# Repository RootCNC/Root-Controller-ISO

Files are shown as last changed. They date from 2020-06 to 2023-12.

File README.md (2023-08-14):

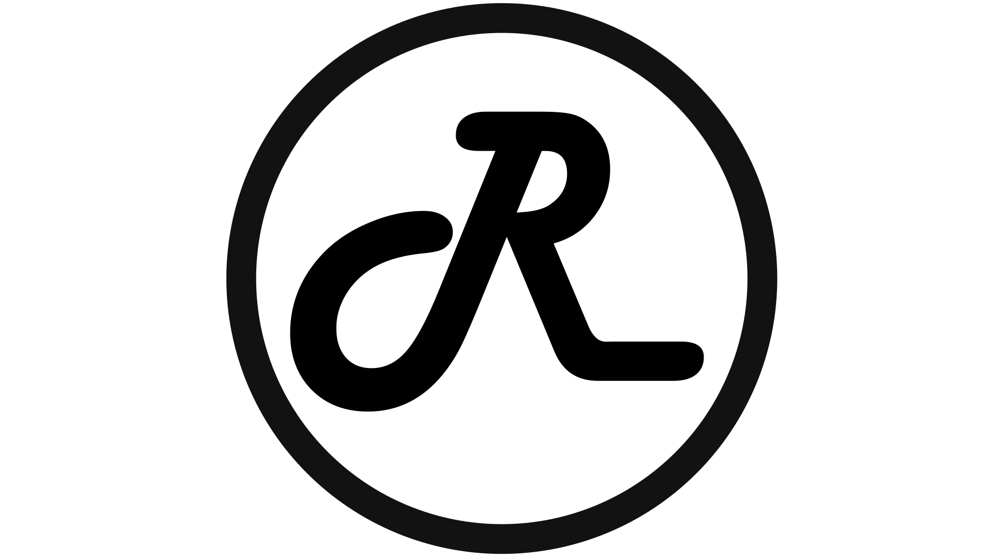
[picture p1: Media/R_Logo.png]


# About
At its core the Root controller is a ESP32 GRBL isolated motion controller (FluidNC). What makes this controller different is the focus of providing **isolated IO** to the **CNC controller**. The controller is designed to accommodate a wide range of operating conditions and machines, to provide ultimate flexibility (its not just a Root CNC Controller).

The controller is designed to isolate the key area of the design to mitigate any nuisance issues when operating in an electrically noisy environment. The design isolates the following areas from one another: Steppers driver outputs (achieved by using externally OPTO isolated drivers), USB, Relays, MOSFETs and RS485. Perfectly suited for the larger CNC machines. 

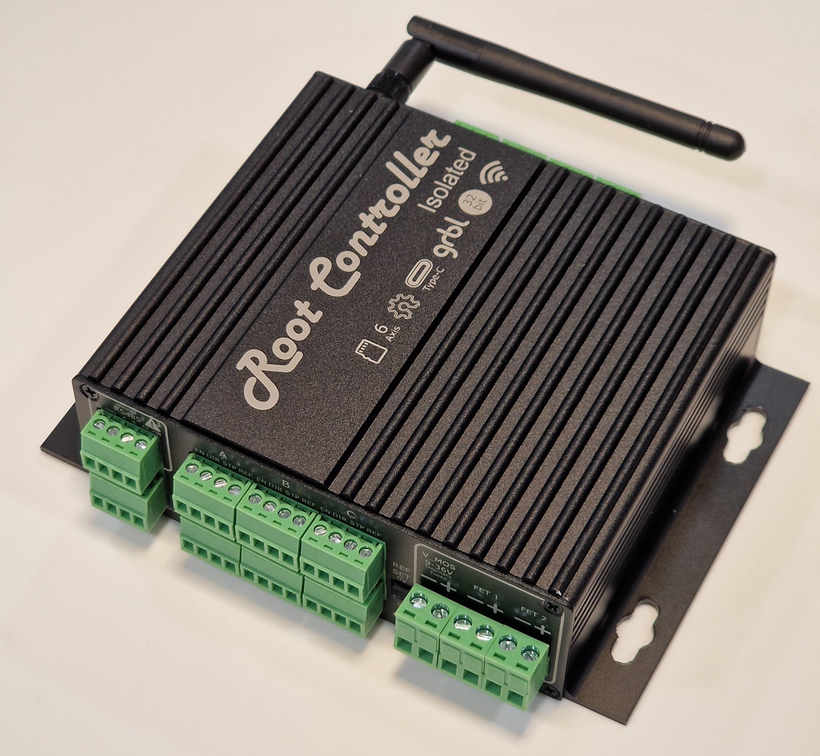
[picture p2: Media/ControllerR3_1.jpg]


## Key features 
1. **6 axis motion control** (Axis ganging can be done via software - 18 digital outputs, can be repurposed)
2. **Wide input voltage** range (9-36V)
3. **Wifi or bluetooth** support for remote control and job loading
4. **SD card**
5. **8 isolated inputs** (supporting NPN inductive switches and Standard NC/NO switches)
6. **2 isolated Relay** outputs for switching high voltage outputs, say a compressor
7. **2 isolated MOSFET**, perfect for driving solenoids for coolant or mist
8. Dedicated **Laser output port**. 
9. **Isolated USB**
10. **Isolated RS485** (Modbus serial port)

## Block Diagram
Root Controller Overview Block Diagram

## Purchase
The Root Controller ISO can be purchased on the Root CNC store
[GOTO SHOP](https://rootcnc.com/product-category/electronics/)

## Demo Video
> Click Image to load youtube video
{.is-info}

Demo Video (https://youtu.be/JiuDgxlzHaU "Video Title")

## Electrical Specification 
Details can be found [**here**](https://wiki.rootcnc.com/en/Root-Controller-ISO/DetailedInfo). If you require additional information I have missed, please contact me and I'll get it added.
## Wiring information
For more information on how to wire and connect the Root Controller to external drives, sensors and other peripherals. please see the Wiki site. [Link to the WIKI](https://wiki.rootcnc.com/en/Root-Controller-ISO/DetailedInfo)
## Software pinouts
To control the hardware the pinout of peripherals needs to be known, the link **[here](https://wiki.rootcnc.com/en/Root-Controller-ISO/DetailedInfo)** is a convenient way to map Input and Output to the software.
## Software Configurations
For basic configurations for your machine, please see the sub folder names "Configurations"

## Mechanical dimensions

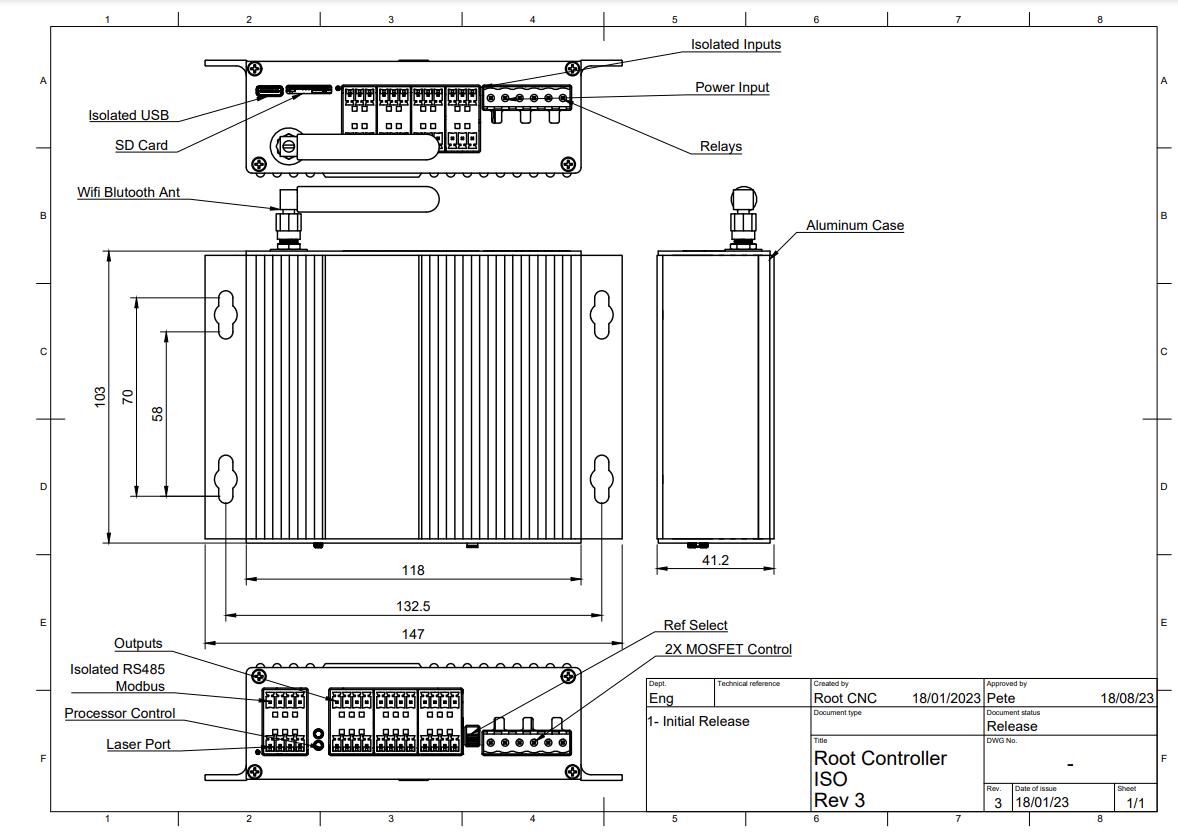
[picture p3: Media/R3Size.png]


## PCB layout

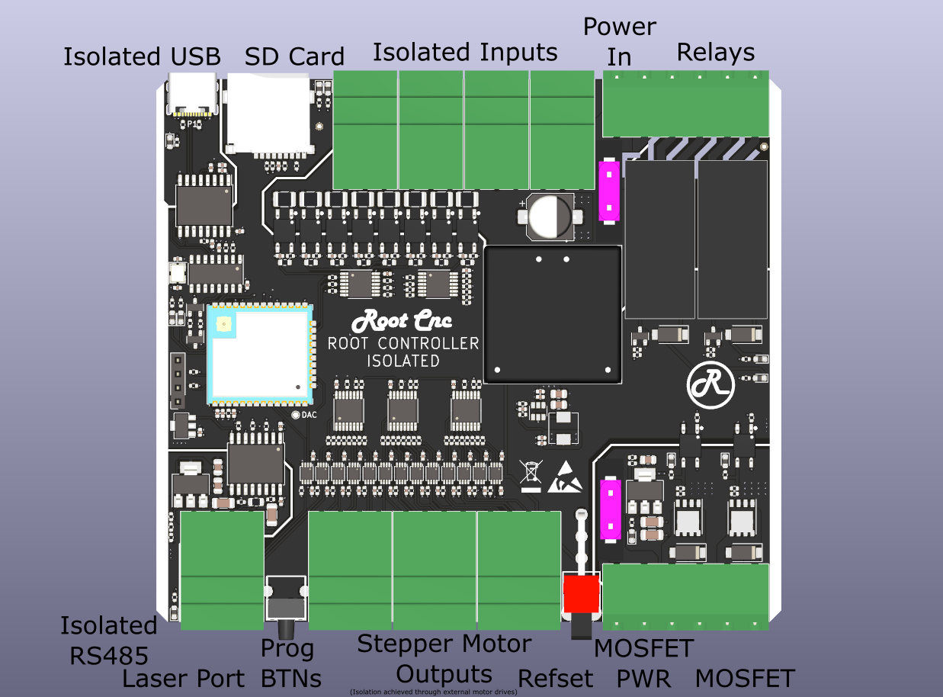
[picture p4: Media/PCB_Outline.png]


## What is Root CNC
For Root CNC project information 
visit [the website](https://rootcnc.com)
## Social links

 1. [Facebook Group](https://www.facebook.com/groups/rootcnc/) 
 2. [Discourse](https://rootcnc.discourse.group/) 
 3. [Discord](https://discord.gg/93Ue5SwthW) Great for quick answer to questions and firmware support
 4. [Thingiverse](https://www.thingiverse.com/sailorpete/designs) 
 5. [Youtube](https://www.youtube.com/c/sailorpete12/)

## License

This project is licensed under the Creative Commons 4.0 license with 
Attribution-NonCommerial-ShareAlike see `LICENSE.txt` for details

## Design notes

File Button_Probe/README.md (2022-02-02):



# About
Easy way to add convenient buttons to your CNC Machine. It offers buttons for common actions like, Hold, Start, Macro. it also offers a easy accessible probe point via 4mm banana plugs
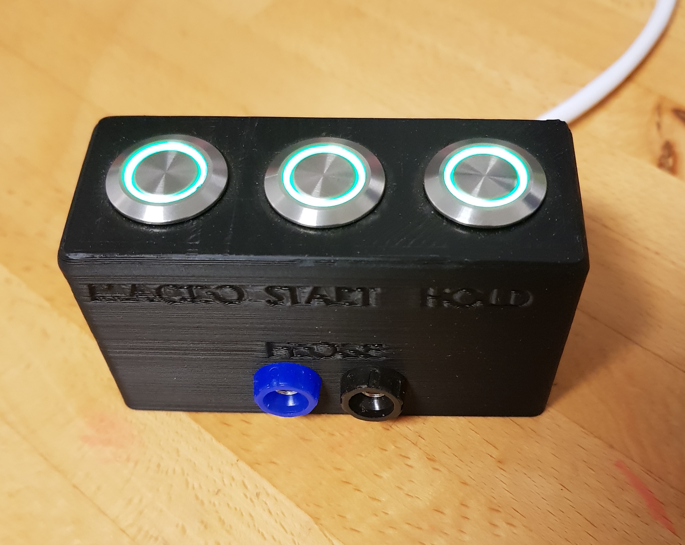
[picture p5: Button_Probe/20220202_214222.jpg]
Root Controller Render


## Key features 
1. Easy breakout and wiring of frequently used buttons and probe mount
2. Built in current limit resistors for LED button

## Require Parts
The product requires parts to be sourced or printed externally
1. Single Pole Single Throw (SPST) Momentary LED Push Button 16mm Dia x3
2. 4mm Banana terminals x2
3. Printed case (Top and bottom)
4. 3mm insert nuts (The kind you use the soldering Iron with) x6
5. 3mm x 6mm Bolts x4
6. 3mm x 10mm Bolts x2

## Purchase
The Root Controller Buttons can be purchased on the Root CNC store
[GOTO SHOP](https://rootcnc.com/product-category/electronics/)

## What is Root CNC
For Root CNC project information 
visit [the website](https://rootcnc.com)
## Social links

 1. [Facebook Group](https://www.facebook.com/groups/rootcnc/) 
 2. [Discourse](https://rootcnc.discourse.group/) 
 3. [Discord](https://discord.gg/93Ue5SwthW) Great for quick answer to questions
 4. [Thingiverse](https://www.thingiverse.com/sailorpete/designs) 
 5. [Youtube](https://www.youtube.com/c/sailorpete12/)

## License

This project is licensed under the Creative Commons 4.0 license with 
Attribution-NonCommerial-ShareAlike see `LICENSE.txt` for details

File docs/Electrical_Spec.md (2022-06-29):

# Root Controller ISO Electrical characteristics
This section is split up into the isolation zones of the controller.

For more information on the different isolation zones, please see the Wiki page tilted "Power" [Link Here](https://wiki.rootcnc.com/en/RootControllerPower)

## Primary PSU
### PSU
This is denoted a `V` and `0V_V` for supply and return respectively on the case sticker.
Power is applied through its own dedicated fused port. 

| **Parameter** | **Min** | **Typ** | **Max** |**Unit**|
|--|--|--|--|--|
| Vin (`V` wrt `0V_V`) | 9 |24|36|V|
|Current (Fuse Protected) (*1)|  |0.86|(*2)|A|
|Input Isolation voltage  [`V` vs `0V`(*3)]| 1.5 |||KV
-   (*1) – This is current draw of the Root CNC controller including worst case power export via output pins. This does not induce the exported power on V pins (Such as powering inductive probes)
- (*2) - Installed fuse is TBD
-  (*3) – 0V is the isolated floating voltage on the Root CNC controller – Do Not connect this to chassis

### Input
The inputs to the Root controller are referenced to the `0V_V` of the Primary PSU. All input are isolated to the rest of the system.

The Input are arranged to accept either an Open-Collector/ Open-Drain switch or a standard mechanical switch. Depending on the Primary PSU voltage this switching current will vary. 
| **Parameter** | **Condition** |**Min** | **Typ** | **Max** |**Unit**|
|--|--|--|--|--|--|
| Switching Current |(*1) |2.7||10|mA|
| |V = 12V ||2.7||mA|
|  |V = 24V ||5.8||mA|
|  |V = 36V ||8.9||mA|

* (1) Over full operating conditions 
# RS485 
This section is denoted by `V_RS` and `0V_RS` respectively for the Power in and 0V for the isolated RS485 port. 

| **Parameter** | **Min** | **Typ** | **Max** |**Unit**|
|--|--|--|--|--|
| Vin (`V_RS`wrt `0V_RS`) | 8.1 |12|36|V|
|Current Draw |  |1.6|2|mA|
|Basic DC Isolation  [`V_RS` vs `0V`]| ||1.517|KV
|Reinforced DC Insulation  [`V_RS` vs `0V`] (*1)| ||0.757|KV
|Basic bipolar AC Isolation  [`V_RS` vs `0V`] (*1)| ||565|V
|Reinforced bipolar AC Insulation  [`V_RS` vs `0V`] (*1)| ||565|V
|Differential Input Threshold Voltage, Vth|-200 |-125|-30|mV
|Input Hysteresis|| 20|| mV
|Input Resistance (A, B) (*2) |96 |150|| kΩ
|Output High Voltage|4.6|4.9||V
|Output Low Voltage||0.1|0.4|V
|Output Short-Circuit Current| 7| |85| mA
|ESD Rating (`A`,`B`)||HMB (+/-2KV)

* (1) Maximum Continuous Working Voltage
* (2) RS485 does not contain a bus termination resistor - place provisioned. The Isolating RS485 has internal thresholds to detect logic levels. 

# Digital Output
Isolation is achieved by using Opto-Isolated Stepper motor drivers

|**Parameter**|**Min**|**Typ**|**Max**|**Unit**|
|--|--|--|--|--|
|Vout (Root controller derived supply)|4.95|5|5.05|V
|Output current|||150|mA
|IOH High-level output current (*1)|||25|mA
|IOL Low-level output current (*1)|||25|mA
|VOH High-level output voltage (*2)|3.8|||V
|VOL Low-level output voltage (*3)|||0.55|V

-   (*1) This parameter makes the Root CNC controller extremely well suited to drive opto-isolated stepper motor drivers (special sauce)
-   (*2) – Over full operating specification and at max current draw (-32mA)
-   (*3) – Over full operating specification and at max current draw (32mA)

# MOSFET Isolation
The Root Controller provides three MOSFET controller switches. These switches have their own dedicated input power supply and can be driven from a separate PSU or the same PSU as `V` to allow for greater flexibility.

| **Parameter** | **Min** | **Typ** | **Max** |**Unit**|
|--|--|--|--|--|
| Vin (`V_F` wrt `0V_F`) | 12|15|36|V|
|Current (Fuse Protected) (*1)|0.001  ||(*2)|A|
* (1) Current is dependant of the peripherals you connect to the controller
* (2) Controller has an internal fuse - Rating is TBD

# Relay 
The Root controller has three NO relays (the Normally closed Pole is not accessible). These are design to allow the user to switch large main powered loads, such as Dust extraction, compressors and even lighting.
| **Parameter** | **Min** | **Typ** | **Max** |**Unit**|
|--|--|--|--|--|
| Switch Voltage DC| ||300|V|
| Switch Voltage AC| ||440|V|
|Contact Resistance|||100|mOhm|
|Switch Current (Resistive Load)|||12|A|
|Max Switch Power|||3000|VA|
|Endurance (Switch Cycles)|||1x10^7||

# USB
The USB port on the Root controller is a Type-C 2.0 UFP. This port is also isolated with the `0V`

| **Parameter** | **Min** | **Typ** | **Max** |**Unit**|
|--|--|--|--|--|
| Voltage (`V_USB` to `0V_USB`) |4.5 |5|5.5|V|
| Current| 5|8|10|mA|
| Data Rate| ||12|Mbps|
|DC Basic Isolation  |||849|V|
|AC Bipolar Basic Isolation  |||849|V|
|AC Unipolar Basic Isolation  |||560|V|

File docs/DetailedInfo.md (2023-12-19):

---
title: About
description: Root Controller ISO About
published: true
date: 2022-03-18T14:52:57.756Z
tags: cnc controller, root controller, motion controller, isolation
editor: markdown
dateCreated: 2022-02-25T22:12:57.077Z
---

# Introduction


At its core the Root controller is a ESP32 GRBL isolated motion controller (FluidNC/ grblHAL). What makes this controller different is the focus of providing  **isolated IO** to the **CNC controller**. The controller is designed to accommodate a wide range of operating conditions and machines, to provide ultimate flexibility (its not just a Root CNC Controller).

The controller is designed to isolate the key area of the design to mitigate any nuisance issues when operating in an electrically noisy environment. The design isolates the following areas from one another: Steppers driver outputs (achieved by using externally OPTO isolated drivers), USB, Relays, MOSFETs and RS485. Perfectly suited for the larger CNC machines. 

## Key features 



1. **6 axis motion control** (Axis ganging can be done via software - 18 digital outputs, can be repurposed)
2. **Wide input voltage** range (9-36V)
3. **WiFi or bluetooth** support for remote control and job loading
4. **SD card**
5. **8 Isolated inputs** (supporting NPN inductive switches and Standard NC/NO switches)
6. **2 Isolated Relay** outputs for switching high voltage outputs, say a compressor
7. **2 isolated MOSFET**, perfect for driving solenoids for coolant or mist
8. Dedicated **Laser output port**. 
9. **Isolated USB**
10. **Isolated RS485** (Modbus serial port)

## Block Diagram
Root Controller Overview Block Diagram

## Demo Video
# Tabs {.tabset} 
> Click Image to load youtube video
{.is-info}

## Rev 3

Demo Video (https://youtu.be/JiuDgxlzHaU "Root Controller Rev 3")

## Rev 2.1/2.0

Demo Video (http://www.youtube.com/watch?v=vrsv_Eusyqc "Root Controller Rev 2")

# Power
The Root controller is segregation into multiple isolation zones to suit the individual needs of the CNC builder. The purpose of these zones is to help isolated areas from interfering with one another. For example the spindle control vs the low noise CNC controller zones. The Root controller is well suited for large CNC machines and plasma cutters.

Carefully consideration should be made when planning the electronics for your CNC machine. As optimal performance is dependent on the type of machine you are building. The information below will aid your design. If you feel information is missing, please send me a message and I’ll clarify and aid you.

The controller has the following major areas of isolation:
1. `V_in ISO` - this is used for all inputs and powering the CNC motion controller.
2. `RS-485 isolation zone` - this provides an isolated RS485 interface to talk to your VFD or other peripherals (more items will be added in the future). This zone is typically powered by the VFD and doesn’t require any additional interfaces or PSUs
3. `MOSFET isolation` - this is a separation isolated zone which comprised of three high power MOSFETs. This is powered from a separate power input and is perfect for controlling device which need power, for example Solenoids, lights etc
4. `Controller reference` - this area is not isolated to the CNC controller. isolation is achieved through the OPTO isolated stepper motor drivers. The laser/ spindle port is also referenced to this area. when using this port, careful consider is required to ensure the other isolation zones are not violated.
5. `Relay zone` - three relay outputs are inherently isolated from everything else and between them self.
6. `USB ISO` - the usb type C connector is isolated from the controller to ensure. This is perfect to ensure your expensive laptop or CNC computer is not directly attached to your machine, this help mitigate fault propagation effecting you machine. 
# Tabs {.tabset}
## Rev 3



## Rev 2.1/2.0
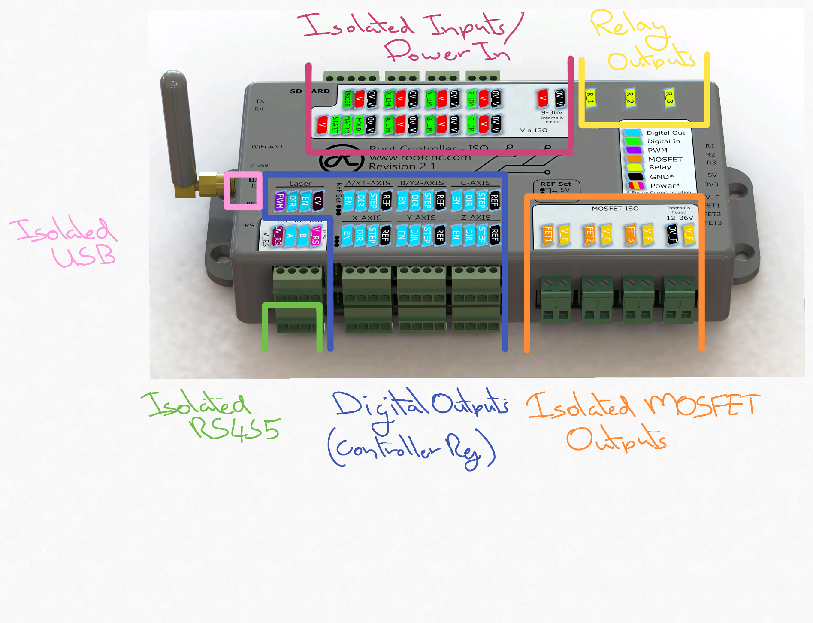
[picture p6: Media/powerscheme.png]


> To ensure optimal performance and noise immunity - please ensure the current return paths and loops are reduced and power zone references are not connected together. E.g. avoid connecting `0V` to `0V_V` 
{.is-warning}

# Powering the controller
Power is applied through the power in connector in the `Vin ISO` zone. The input requires a supply voltage of anything between 12-36v. 

This power supply is internally fused for added protection.

The minimum PSU capacity should greater then `8 watts` to power the controller.

The voltage applied to the controller through this connector is also applied to the controllers inputs power pins. This is useful when powering external sensors, such as inductive probes. The inputs power pins are fused with the same fuse as the main input power connector. 

# Tabs {.tabset}
## Rev 3



## Rev 2.1/2.0
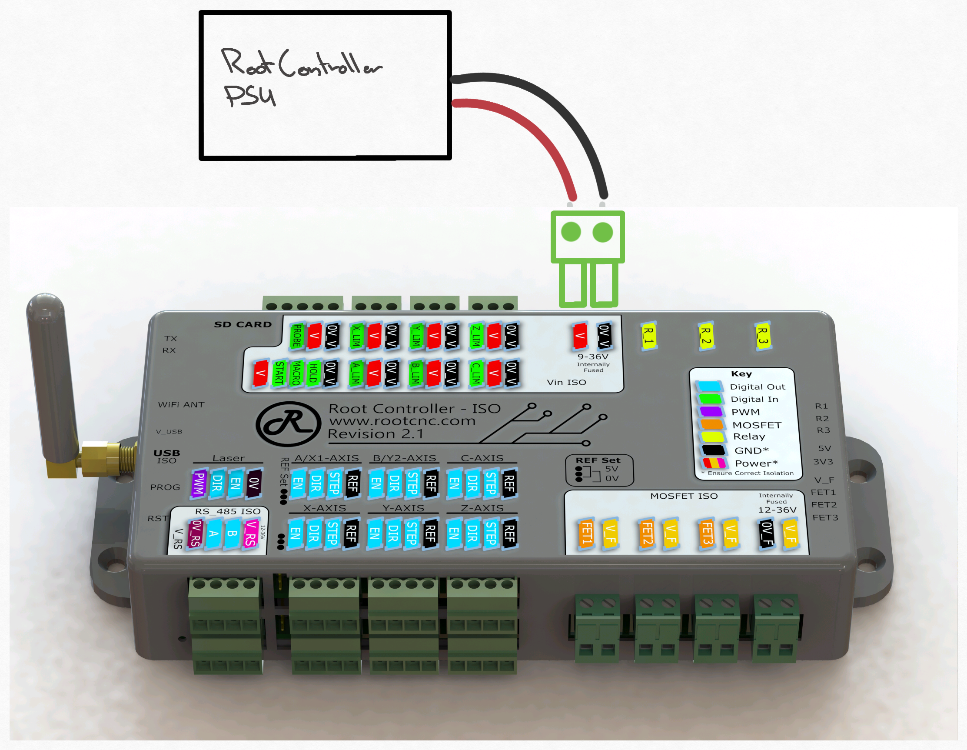
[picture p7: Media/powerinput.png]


# Stepper control
The Root Controller is specifically designed to control **OPTO isolated external stepper motor drivers**. The reason for this is due to their high current demands of their logic inputs on the motor driver, these are typically around 10-20mA per input (enable signals are typically lower as these do tend not to toggle). These sort of current demands normally exceeds the max electronic IC package current. Exceeding these values can impact the life of the electronic products - the Root controller ISO has been designed to take this into account and will happily supply the max current across all its outputs and provide a long life for the electronics.

The Root controller Rev `2.1` and onwards supports both `common Anode` and `common Cathode` external motor drivers, with the use of the `ref set` settings. 

| Drive type | Rev 3 | Rev 2.1 | Rev 2.0  |
|---|---|---|---|
| Common Annode  | Yes | Yes | NO |
| Common Cathode | Yes | Yes | Yes |

>Some drivers might expose both anode and cathode per input, if this is the case then the wiring will need to be configured into either common anode or common cathode. please see example wiring configurations for more information
{.is-info} 

## Stepper Driver Outputs
The Root controller support six software configurable stepper motor outputs. These are accessable via a 4 port connector, which are wired identically.
## Tabs {.tabset}
### Rev 3



### Rev 2.1/2.0


When not using these ports for the stepper motor controller, then the remaining ports can be reconfigured in software to support discrete outputs.

## Ref Set 
> The Root Controller has two configurable references, either 0V or 5V to set the refernece point for either common anode or cathode stepper motor wiring. please ensure these are correctly configured. More information below. (Rev 2.1 and onwards) {.is-info} 

## Tabs {.tabset}
### Rev 3



### Rev 2.1
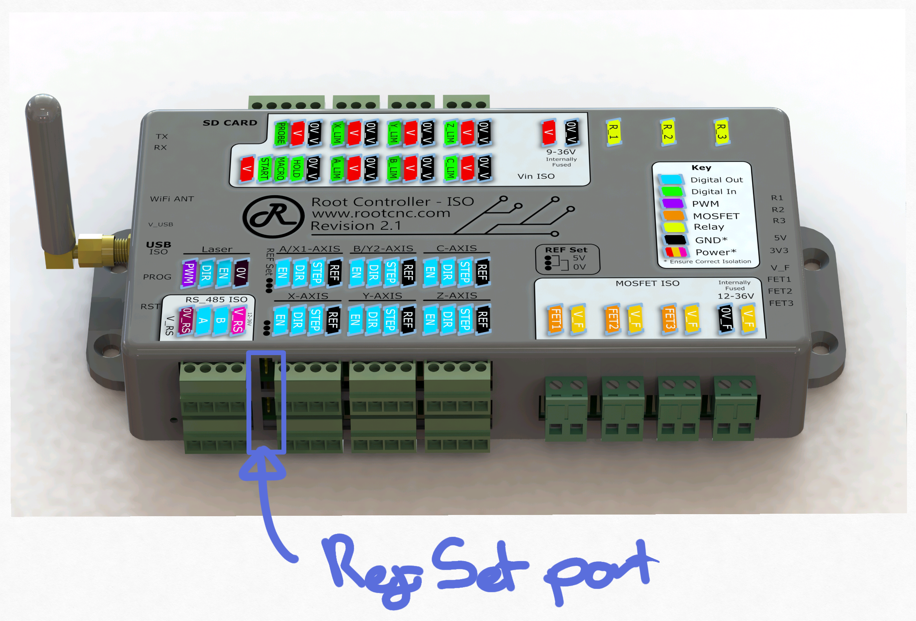
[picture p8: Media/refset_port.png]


Both headers on the Root Controller need to be set correctly in order for correct operation, these are denoted as `ref set` on the controller label. You can mix the top and bottom reference points but you’ll need to ensure the three outputs per layer are set correctly with the corresponding outputs. Its recommended to set the ref set points to same configurations.

- Ref set 1 - sets the reference point for axis outputs X, Y, Z
- Ref set 2 - sets the reference point for axis outputs A, B, C
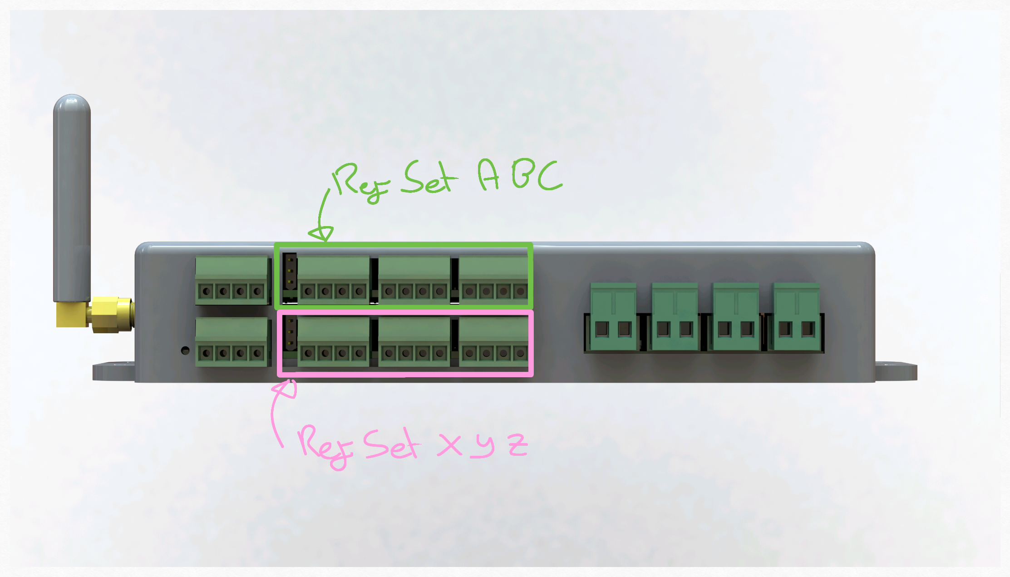
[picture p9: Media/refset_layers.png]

> Please note these outputs are software configurable. The Root 3 onwards will use either axis outputs of A, B, C to be the second Y (YII) axis. If you are planning on using the root controller for other style of machines; the software supports up to two outputs per axis. For example the MPCNC Which has XII and YII which will use ports A,B.{.is-info} 

### Rev 2.0
>` Rev 2.0` only supports a common cathode (0V reference) {.is-warning}

### Beta Card

> Beta card can accommodate both common anode and common cathode by default{.is-info} 

## Stepper Motor Driver Wiring
### 5V reference (Common Anode)
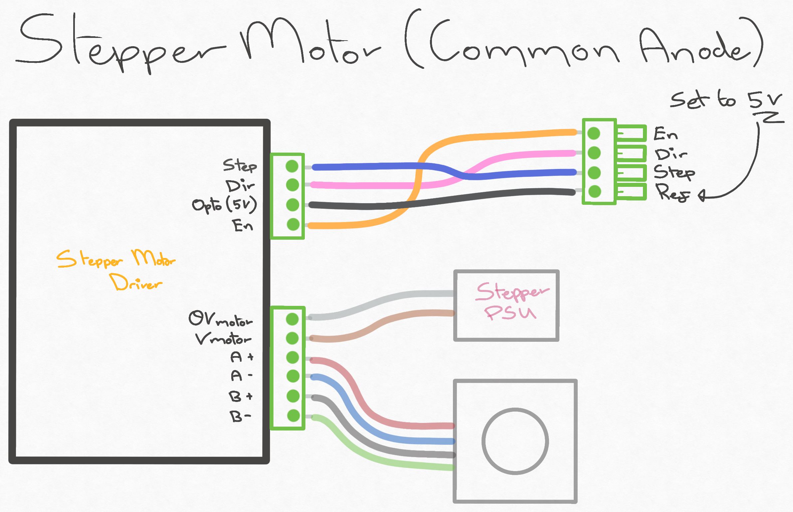
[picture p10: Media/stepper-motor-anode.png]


Below is a list of known external motor drivers to work in the common anode configuration:
* DM320
* DM332

Using this configuration results in the logic being inverted - please configure the software to be either Rising or falling edge triggered or your machine could be half a step out continuously 

### 0V reference (Common Cathode)
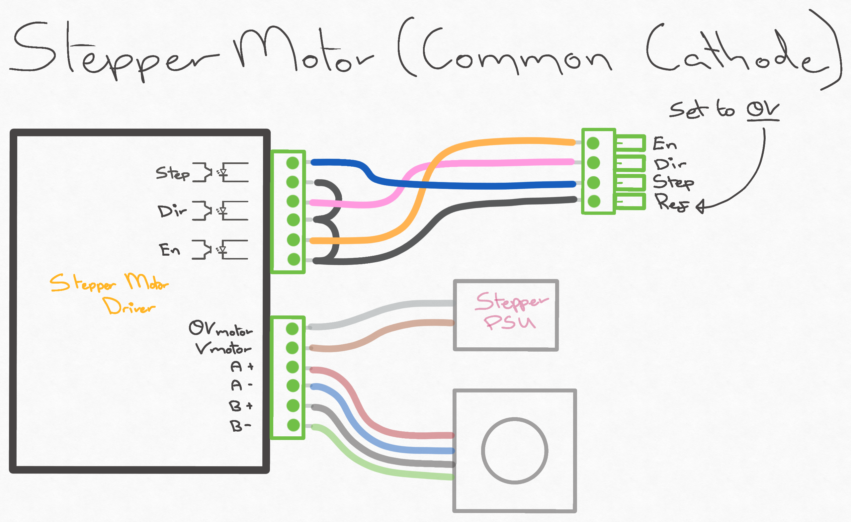
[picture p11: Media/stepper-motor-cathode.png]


Below is a list of known external motor driver to work in the common cathode arrangement

>  My Root 4 and 4 Lite both use the common cathode setup

* DM542
* DM556
* DM860

#### Fuildnc motor configuration (Common Cathode)

#### Tabs {.tabset}

##### X Motor


```
      x:
        steps_per_mm: 160.000
        max_rate_mm_per_min: 4500.000
        acceleration_mm_per_sec2: 500.000
        max_travel_mm: 100
        soft_limits: true
        homing:
          cycle: 1
          positive_direction: true
          mpos_mm: 100
          feed_mm_per_min: 100.000
          seek_mm_per_min: 800.000
          settle_ms: 500
          seek_scaler: 1.100
          feed_scaler: 1.100
    
        motor0:
          limit_neg_pin: NO_PIN
          limit_pos_pin: NO_PIN
          limit_all_pin: NO_PIN
          hard_limits: true
          pulloff_mm:1.000
          standard_stepper:
            step_pin: I2SO.7:low 
            direction_pin: I2SO.5:low 
            disable_pin: I2SO.3:high
```

Motor definition for the X motor port

##### Y Motor



```
  y:
    steps_per_mm: 160.000
    max_rate_mm_per_min: 4500.000
    acceleration_mm_per_sec2: 500.000
    max_travel_mm: 100.000
    soft_limits: true
    homing:
      cycle: 1
      positive_direction: true
      mpos_mm: 100
      feed_mm_per_min: 100.000
      seek_mm_per_min: 800.000
      settle_ms: 500
      seek_scaler: 1.100
      feed_scaler: 1.100

    motor0:
      limit_neg_pin: NO_PIN
      limit_pos_pin: NO_PIN
      limit_all_pin: NO_PIN
      hard_limits: true
      pulloff_mm:1.000
      standard_stepper:
        step_pin: I2SO.12:low 
        direction_pin: I2SO.10:low 
        disable_pin: I2SO.8:high
```

Motor definition for the Y motor port

##### Z Motor



```
  z:
    steps_per_mm: 160.000
    max_rate_mm_per_min: 4500.000
    acceleration_mm_per_sec2: 500.000
    max_travel_mm: 100.000
    soft_limits: true
    homing:
      cycle: 1
      positive_direction: true
      mpos_mm: 100
      feed_mm_per_min: 100.000
      seek_mm_per_min: 800.000
      settle_ms: 500
      seek_scaler: 1.100
      feed_scaler: 1.100

    motor0:
      limit_neg_pin: NO_PIN
      limit_pos_pin: NO_PIN
      limit_all_pin: NO_PIN
      hard_limits: true
      pulloff_mm:1.000
      standard_stepper:
        step_pin: I2SO.18:low 
        direction_pin: I2SO.16:low 
        disable_pin: I2SO.14:high
```

Motor definition for the Z motor port

##### A Motor



```
  a:
    steps_per_mm: 160.000
    max_rate_mm_per_min: 4500.000
    acceleration_mm_per_sec2: 500.000
    max_travel_mm: 100.000
    soft_limits: true
    homing:
      cycle: 1
      positive_direction: true
      mpos_mm: 100
      feed_mm_per_min: 100.000
      seek_mm_per_min: 800.000
      settle_ms: 500
      seek_scaler: 1.100
      feed_scaler: 1.100

    motor0:
      limit_neg_pin: NO_PIN
      limit_pos_pin: NO_PIN
      limit_all_pin: NO_PIN
      hard_limits: true
      pulloff_mm:1.000
      standard_stepper:
        step_pin: I2SO.6:low 
        direction_pin: I2SO.4:low 
        disable_pin: I2SO.2:high
```

Motor definition for the A motor port

##### B Motor



```
  b:
    steps_per_mm: 160.000
    max_rate_mm_per_min: 4500.000
    acceleration_mm_per_sec2: 500.000
    max_travel_mm: 100.000
    soft_limits: true
    homing:
      cycle: 1
      positive_direction: true
      mpos_mm: 100
      feed_mm_per_min: 100.000
      seek_mm_per_min: 800.000
      settle_ms: 500
      seek_scaler: 1.100
      feed_scaler: 1.100

    motor0:
      limit_neg_pin: NO_PIN
      limit_pos_pin: NO_PIN
      limit_all_pin: NO_PIN
      hard_limits: true
      pulloff_mm:1.000
      standard_stepper:
        step_pin: I2SO.13:low 
        direction_pin: I2SO.11:low 
        disable_pin: I2SO.9:high
```

Motor definition for the B motor port

##### C Motor



```
  c:
    steps_per_mm: 160.000
    max_rate_mm_per_min: 4500.000
    acceleration_mm_per_sec2: 500.000
    max_travel_mm: 100.000
    soft_limits: true
    homing:
      cycle: 1
      positive_direction: true
      mpos_mm: 100
      feed_mm_per_min: 100.000
      seek_mm_per_min: 800.000
      settle_ms: 500
      seek_scaler: 1.100
      feed_scaler: 1.100

    motor0:
      limit_neg_pin: NO_PIN
      limit_pos_pin: NO_PIN
      limit_all_pin: NO_PIN
      hard_limits: true
      pulloff_mm:1.000
      standard_stepper:
        step_pin: I2SO.19:low 
        direction_pin: I2SO.17:low 
        disable_pin: I2SO.15:high
```

Motor definition for the Y motor port

##### X Dual Motors
Ganging two motors together can be implemented with the following motor definition:

> (In this example I use the X Motor and A motor port){.is-info}
```
  x:
    steps_per_mm: 160.000
    max_rate_mm_per_min: 4500.000
    acceleration_mm_per_sec2: 500.000
    max_travel_mm: 100
    soft_limits: true
    homing:
      cycle: 1
      positive_direction: true
      mpos_mm: 100
      feed_mm_per_min: 100.000
      seek_mm_per_min: 800.000
      settle_ms: 500
      seek_scaler: 1.100
      feed_scaler: 1.100

    motor0:
      limit_neg_pin: NO_PIN
      limit_pos_pin: NO_PIN
      limit_all_pin: NO_PIN
      hard_limits: true
      pulloff_mm:1.000
      standard_stepper:
        step_pin: I2SO.7:low 
        direction_pin: I2SO.5:low 
        disable_pin: I2SO.3:high
    motor1:
      limit_neg_pin: NO_PIN
      limit_pos_pin: NO_PIN
      limit_all_pin: NO_PIN
      hard_limits: true
      pulloff_mm:1.000
      standard_stepper:
        step_pin: I2SO.6:low 
        direction_pin: I2SO.4:low 
        disable_pin: I2SO.2:high
```
> Any axis can have ganged motors! upto a total of 6 motors per controller. This is an example axis configuration.{.is-info}

##### Y Dual Motors

Ganging two motors together can be implemented with the following motor definition. This configuration is used on the Root CNC series.
> (In this example I use the Y Motor and B motor port){.is-info}
```
  y:
    steps_per_mm: 160.000
    max_rate_mm_per_min: 4500.000
    acceleration_mm_per_sec2: 500.000
    max_travel_mm: 100.000
    soft_limits: true
    homing:
      cycle: 1
      positive_direction: true
      mpos_mm: 100
      feed_mm_per_min: 100.000
      seek_mm_per_min: 800.000
      settle_ms: 500
      seek_scaler: 1.100
      feed_scaler: 1.100

    motor0:
      limit_neg_pin: NO_PIN
      limit_pos_pin: NO_PIN
      limit_all_pin: NO_PIN
      hard_limits: true
      pulloff_mm:1.000
      standard_stepper:
        step_pin: I2SO.12:low 
        direction_pin: I2SO.10:low 
        disable_pin: I2SO.8:high
    motor1:
      limit_neg_pin: NO_PIN
      limit_pos_pin: NO_PIN
      limit_all_pin: NO_PIN
      hard_limits: true
      pulloff_mm:1.000
      standard_stepper:
        step_pin: I2SO.13:low 
        direction_pin: I2SO.11:low 
        disable_pin: I2SO.9:high
```
> Any axis can have ganged motors! upto a total of 6 motors per controller. This is an example axis configuration.{.is-info}

#### grblHAL motor configuration (Common Cathode)

#### Tabs {.tabset}

##### X Motor
Comming soon

##### Y Motor
Comming soon

##### Z Motor
Comming soon

##### A Motor
Comming soon

##### B Motor
Comming soon

##### C Motor
Comming soon

# Inputs
The Root controller ISO has isolated inputs which are referenced to the Vin section of the card. Please take note of the isolation boundaries when connecting up the inputs.

The Controller is designed to support normal volt-free switch; such as mechanical switches, either NC (normally closed) or NO (normally open); And/Or NPN inductive sensors. All inputs are electrically the same. For ease of wiring, all axis limit inputs have the same connector and pin out. 

The inputs which are used for “start”, “hold” and “macro” do have a different connector, so please take note of the difference in wiring. Again easy to wiring, Root CNC offer a easy button/ probe point PCB. These can be purchased from the store or downloaded from GitHub.

All inputs are software configured and can be repurposed.

| | Rev 3 | Rev 2.1 | Rev 2.0  |
|---|---|---|---|
| Axis Inputs | 6 | 6 | 6 |
| Probe Input | 1 | 1 | 1 |
| User Configurable  | 1 | 3 | 3 |

> Please note all input listed in the table are software configurable inputs which can be used for any function.



- axis inputs (one per axis, min and max can be combined onto on input. Please see the end stop section for more information)
- x1 probe point (used to auto tool height correction of edge finding)
- user configurable inputs (these are typically used for GRBL control signals such as Start, Hold, Reset and Macros.

## Endstops
As mentioned in the pervious section, the Root controller is designed to accommodate voltage free switches, such as mechanical lever switches or NPN inductive switches.

Each input can have two sensors/ switches connected to it, these are typically used on axis with min and max limit switches.

### Inductive Probe Wiring 
> NPN Inductive Switch sensor ONLY {.is-info}

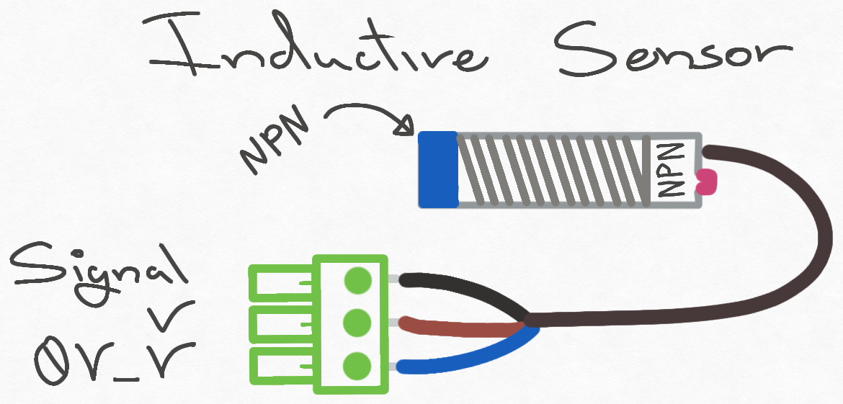
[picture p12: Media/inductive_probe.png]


### Inductive Probe Min & Max Wiring 
Image comming soon

### Basic Endstop Wiring
In this basic configuration, either NO (Normally Open) Or NC (Normally Closed) switches can be used
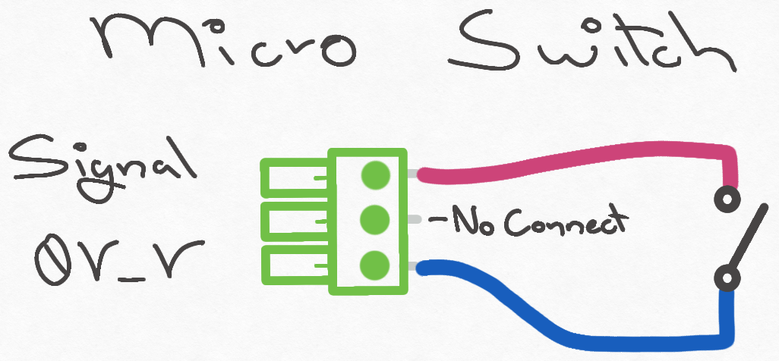
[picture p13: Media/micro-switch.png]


### Endstop wiring Min & Max (NO)
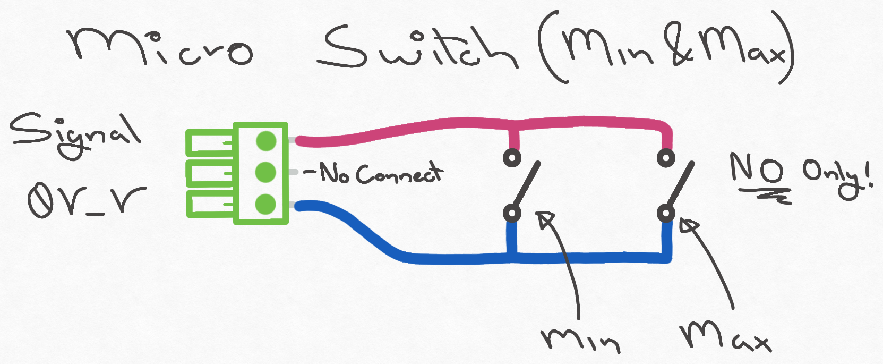
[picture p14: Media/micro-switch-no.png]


### Endstop wiring Min & Max (NC)
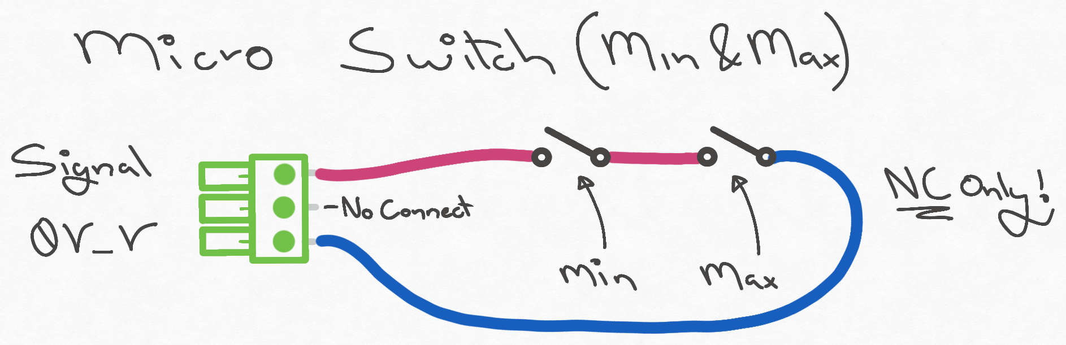
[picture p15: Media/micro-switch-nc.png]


> Please note REV 2.1/REV 2.0 - NC switches are not recommend on `Y_lim`. IF YOU INTEND TO FLASH THE ROOT CONTROLLER WHILST BEING INSTALLED IN A SYSTEMS. pulling these pins LOW stops the programming routing. If you do use NC switched: then, please ensure these are disconnected piror to programming. 
{.is-warning}

# Outputs
Aside from the digital outputs of the stepper driver port (Please see # Stepper control for more information). The Root Controller has the additional outputs:

| | Rev 3 | Rev 2.1 | Rev 2.0 |
|---|---|---|---|
|  MOSFET output (Isolated control) | 2 | 3 | 3 |
| High power relays | 2 | 3 | 3 |
| Laser/ spindle port (none isolated) | PWM, DIR, EN | PWM, DIR, EN | PWM, DIR, EN  |

- MOSFET output, great for turning lights or solenoids  on/off
- High power relays output, perfectly suited for turning shop vacs on or dust extractors
- Laser/ spindle port, perfect for controlling a PWM device

## MOSFETS
The Root controller has a number of high power MOSFETs which can be used to switch the power to a number of device, such as solenoids, lights and DC motors. 

The power supply is fed by its dedicated power connector. The input power is internally fused for added protection. The supply can be separate or tied to other supplies depending on your configuration.

The MOSFET area is perfectly suited for switching inductive loads such a solenoids or relays. 

| | Rev 3 | Rev 2.1 | Rev 2.0 |
|---|---|---|---|
|  PWM 															  | 1 (FET_1) | 2 (FET_1/2)  | 2 (FET_1/2) |
|  ON/ OFF controller								  | 1 | 1 | 1 |
|  **Total** 														  | **2** | **3** | **3** |

MOSFET control = on/off control and PWM control (Hardware dependant)

## Tabs {.tabset}
### Rev 3



> Please note depending on the software configuration, not all MOSFET or RELAY output can be used at the same time.
{.is-info}
### Rev 2.1/2.0


MOSFET control
- FET_1 - on/off control
- FET_2 - on/off control 
- FET_3 - on/off control

> Please note depending on the software configuration, not all MOSFET or RELAY output can be used at the same time.
{.is-info}

## Relay output 
The Root controller has a number relays outputs which can be used to switch high power loads, such as dust extractors, fume extractors and vacum cleaners. 

These relays are capable of switching mains power with a current of 13A.

| | Rev 3 | Rev 2.1 | Rev 2.0 |
|---|---|---|---|
| On/ Off control Relau | 2 | 3 | 3 |

## Tabs {.tabset}
### Rev 3



> Please note depending on the software configuration, not all MOSFET or RELAY output can be used at the same time.
{.is-info}
### Rev 2.1/2.0



> Please note depending on the software configuration, not all MOSFET or RELAY output can be used at the same time.
{.is-info}

## PWM laser/ Spindle output
The Root controller has a discrete output port which can be used to control a number of different devices. For example: lasers, and discrete control spindles.

Laser/ Spindle control
- EN - on/off control
- DIR - on/off control 
- PWM - on/off control & PWM Control

## Tabs {.tabset}
### Rev 3



### Rev 2.1/2.0


> For spindle control, it is advised you use a MODBUS/ RS485 VFD and communicated through the isolated spindle interface.
{.is-info}

> This port is NOT isolated so careful consideration is needed when connecting external devices to ensure the isolation zones are not violated
{.is-warning}

# Isolated RS485
The Root controller offers a fully isolated RS485/ MODBUS interface. This interface allows communication between the controller and a VFD spindle motor (OR other device - Software dependant).

This interface is intended to be to a small isolated area which is powered form the VFD or downstream connected device. for full operating range, please see the electrical specification below.

All versions of the Root Controller ISO offer the isolated RS485 interface



> Please note this interface will not work unless externally powered {.warning}

Here is an example of the wiring for the RS485 interface on a huanyang VFD

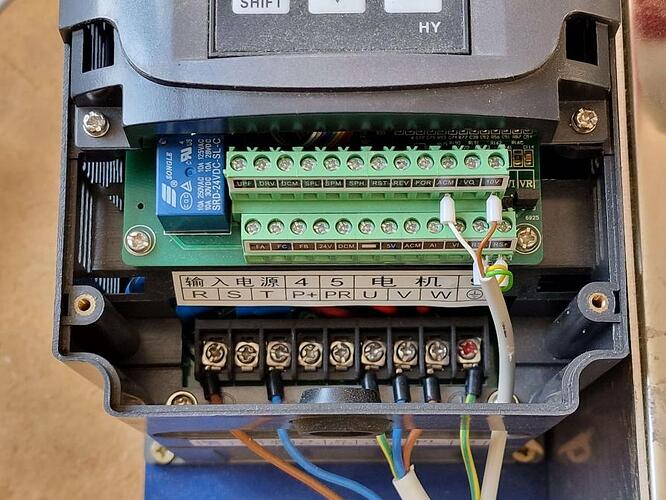
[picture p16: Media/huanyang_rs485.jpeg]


# SD CARD

The Root controller has expandable storage option in the form of an SD card. files can be sent over WIFI and stored on the SD for later use. this is particularly handy when running repetitive jobs. files can be accessed from a web browser over your local network.

For better compatibility, please use the older SD card rather than the newer ones.



All versions of the Root Controller ISO offer a SD card interface

To enable the code please use the following in the configuration

# Tabs {.tabset}
## Fluidnc

```
spi:
  miso_pin: gpio.19
  mosi_pin: gpio.23
  sck_pin: gpio.18

sdcard:
  card_detect_pin: NO_PIN
  cs_pin: gpio.5
```
## grblHAL

# WIFI / Blutooth

The Root controller offers wireless capability. this allows controller of the machine through your local network or via a mobile phone and blutooth. 

As EMC and isolation is a concern; careful positioning and placement of the antenna is critical for optimum performance. The Root Controller had implemented an internal antenna with the goal to reduce the cost of the controller. but this led to poor WIFI coverage; for this reason, the new versions of the Root controller offer an external antenna with can be extended using a standard SMA extension lead.



> Please note: the outer shield of the Antenna is connected to an internal reference plane. you **MUST NOT** connect this to Chassis or any other return planes as this will ruin your isolated setup. you will note the antenna port on the newer Rev 3 and onwards controllers has isolation washer between the case and the connector. This is to stop this connection from happening. If you intend to extend this internal for better antenna performance, or outside and electrical cabinet  - please ensure the isolation boundaries of isolation are kept. {.warning}

| | Rev 3 | Rev 2.1 | Rev 2.0 | Beta Card |
|---|---|---|---|---|
| WIFI Antenna  | External  | External  | Internal  | Internal  |

# Pin mapping
The Root controller comes in different forms, please select the tab that matches your hardware revision 
# Tabs {.tabset}
## ISO Rev 3

### I2S Output Port Mapping
I2S Bus is purely outputs ONLY.
| **Port**  |  **Description** |  **Port**  |  **Description** |  **Port**  |  **Description** |
|---|---|---|---|---|---|
| **I2S_0** | LASER_DIR | **I2S_8**  | Y_EN | **I2S_16** | Z_DIR |
| **I2S_1** | LASER_EN | **I2S_9**  | B_EN | **I2S_17** | C_DIR |
| **I2S_2** | A_EN | **I2S_10** | Y_DIR | **I2S_18** | Z_STEP |
| **I2S_3** | X_EN | **I2S_11** | B_DIR  		 | **I2S_19** | C_STEP |
| **I2S_4** | A_DIR			 | **I2S_12** | Y_STEP | **I2S_20** | RELAY_2 |
| **I2S_5** | X_DIR | **I2S_13** | B_STEP | **I2S_21** | RELAY_1 |
| **I2S_6** | A_STEP | **I2S_14** | Z_EN | **I2S_22** | FET_2 |
| **I2S_7** | X_STEP | **I2S_15** | C_EN | **I2S_23** | NOT USED |
{.dense}

### ESP32 Mapping
|**Port**| **Description**|**Port**| **Description**|**Port**| **Description**|
|--|--|--|--|--|--|
|**GPIO2**|P-PIN 	|**GPIO17**|RS_485_TX |**GPIO27**|Z-PIN  |  
|**GPIO4**|RS_485_DE_RE 	|**GPIO18**|SD_CLK |**GPIO32**|Y-PIN | 
|**GPIO5**|SD_CS 	|**GPIO19**|SD_MISO |**GPIO33**|LASER PWM |
|**GPIO12**|SHIFT_DATA 	|**GPIO21**|SHIFT_STR_CLK |**GPIO34**|X-PIN |
|**GPIO13**|FET_1 (PWM) |**GPIO22**|SHIFT_CLK |**GPIO35**| B-PIN |
|**GPIO14**|C-PIN 	|**GPIO23**|SD_MOSI |**GPIO36**|INTERNAL TEST POINT |
|**GPIO15**|*-PIN 	|**GPIO25**|INTERNAL TEST POINT |**GPIO39**|INTERNAL TEST POINT |
|**GPIO16**|RS_485_RX 	|**GPIO26**|A-PIN |||
{.dense}

## ISO Rev 2.0/2.1
> This list support the revision 2.0 Onwards. If you're after an earlier version pin out please see the version history on Github 
{.is-info}
### I2S Output Port Mapping
I2S Bus is purely outputs ONLY.
|**Port**| **Description**|**Port**| **Description**|**Port**| **Description**|**Port**| **Description**|
|--|--|--|--|--|--|--|--|--|--|
|**I2S_0**	|X_EN_PIN |**I2S_8**|Z_EN_PIN |**I2S_16**|	SPINDLE_DIR |**I2S_24**|	B_EN_PIN |
|**I2S_1**	|X_DIRECTION_PIN |**I2S_9**|Z_DIRECTION_PIN |**I2S_17**|	SPINDLE_EN |**I2S_25**|	B_DIRECTION_PIN|
|**I2S_2**	|X_STEP_PIN |**I2S_10**|	Z_STEP_PIN |**I2S_18**|	SPARE_1 |**I2S_26**|	B_STEP_PIN |
|**I2S_3**	|X_CS - NOT USED |**I2S_11**|	Z_CS - NOT USED|**I2S_19**|	SPARE_2 |**I2S_27**|	B_CS - NOT USED|
|**I2S_4**	|Y_EN_PIN |**I2S_12**|	FET_1 |**I2S_20**|	A_EN_PIN |**I2S_28**|	C_EN_PIN |
|**I2S_5**	|Y_DIRECTION_PIN |**I2S_13**|	RELAY_1 |**I2S_21**|	A_DIRECTION_PIN|**I2S_29**|	C_DIRECTION_PIN|
|**I2S_6**	|Y_STEP_PIN |**I2S_14**|	RELAY_2 |**I2S_22**|	A_STEP_PIN |**I2S_30**|	C_STEP_PIN |
|**I2S_7**	|Y_CS - NOT USED |**I2S_15**|	RELAY_3 |**I2S_23**|	A_CS - NOT USED|**I2S_31**|	C_CS - NOT USED|
{.dense}

### ESP32 Mapping
|**Port**| **Description**|**Port**| **Description**|**Port**| **Description**|
|--|--|--|--|--|--|
|**GPIO2**|Y-PIN 	|**GPIO17**|RS_485_TX |**GPIO27**|PROBE-PIN  |  
|**GPIO4**|RS_485_DE_RE 	|**GPIO18**|SD_CLK |**GPIO32**|B-PIN | 
|**GPIO5**|SD_CS 	|**GPIO19**|SD_MISO |**GPIO33**|FET_2 |
|**GPIO12**|SHIFT_DATA 	|**GPIO21**|SHIFT_STR_CLK |**GPIO34**|GRBL_MACRO |
|**GPIO13**|FET_3 	|**GPIO22**|SHIFT_CLK |**GPIO35**| A-PIN |
|**GPIO14**|C-PIN 	|**GPIO23**|SD_MOSI |**GPIO36**|GRBL_HOLD |
|**GPIO15**|Z-PIN 	|**GPIO25**|DAC_OUT/PWM |**GPIO39**|GRBL_START |
|**GPIO16**|RS_485_RX 	|**GPIO26**|X-PIN |||
{.dense}

# Electrical Specification 
If you require additional information I have missed, please contact me and I'll get it added.
# Tabs {.tabset} 
## Rev 3/2.1/2.0
### Primary PSU
This is denoted a `V` and `0V_V` for supply and return respectively on the case sticker.
Power is applied through its own dedicated fused port. 
| **Parameter** | **Min** | **Typ** | **Max** |**Unit**|
|---|---|---|---|---|
| Vin (`V` wrt `0V_V`) | 9 | 24 | 36 | V |
|Current (Fuse Protected) [^1]|  |0.86|5[^2]|A|
|Input Isolation voltage  [`V` vs `0V`[^3]]| 1.5 |||KV|
{.dense}

[^1]: This is current draw of the Root CNC controller including worst case power export via output pins. This does not induce the exported power on V pins (Such as powering inductive probes)
[^2]: Installed Micro fuse is 5A 
[^3]: 0V is the isolated floating voltage on the Root CNC controller – Do Not connect this to chassis

### Input
The inputs to the Root controller are referenced to the `0V_V` of the Primary PSU. All input are isolated to the rest of the system.
> To ensure optimal performance and noise immunity - please ensure the current return paths and loops are reduced and power zone references are not connected together. E.g. avoid connecting `0V` to `0V_V` 
{.is-warning}

The Input are arranged to accept either an Open-Collector/ Open-Drain switch or a standard mechanical switch. Depending on the Primary PSU voltage this switching current will vary. 
| **Parameter** | **Condition** |**Min** | **Typ** | **Max** |**Unit**|
|--|--|--|--|--|--|
| Switching Current |(*1) |2.7||10|mA|
| |V = 12V ||2.7||mA|
|  |V = 24V ||5.8||mA|
|  |V = 36V ||8.9||mA|
{.dense}

* (1) Over full operating conditions 
### RS485 
This section is denoted by `V_RS` and `0V_RS` respectively for the Power in and 0V for the isolated RS485 port. 

| **Parameter** | **Min** | **Typ** | **Max** |**Unit**|
|--|--|--|--|--|
| Vin (`V_RS`wrt `0V_RS`) | 8.1 |12|36|V|
|Current Draw |  |1.6|2|mA|
|Basic DC Isolation  [`V_RS` vs `0V`]| ||1.517|KV
|Reinforced DC Insulation  [`V_RS` vs `0V`] [^4] || 0.757||KV
|Basic bipolar AC Isolation  [`V_RS` vs `0V`] [^4]| ||565|V
|Reinforced bipolar AC Insulation  [`V_RS` vs `0V`] [^5]| ||565|V
|Differential Input Threshold Voltage, Vth|-200 |-125|-30|mV
|Input Hysteresis|| 20|| mV
|Input Resistance (A, B) (*2) |96 |150|| kΩ
|Output High Voltage|4.6|4.9||V
|Output Low Voltage||0.1|0.4|V
|Output Short-Circuit Current| 7| |85| mA
|ESD Rating (`A`,`B`)||HMB (+/-2KV)|
{.dense}

[^4]:  Maximum Continuous Working Voltage
[^5]:  RS485 does not contain a bus termination resistor - place provisioned. The Isolating RS485 has internal thresholds to detect logic levels. 

### Digital Output (Stepper Outputs)

>Isolation is achieved by using Opto-Isolated Stepper motor drivers such as "DM556"
{.is-info}

|**Parameter**|**Min**|**Typ**|**Max**|**Unit**|
|--|--|--|--|--|
|Vout (Root controller derived supply)|4.95|5|5.05|V
|Output current|||150|mA
|IOH High-level output current [^6]|||25|mA
|IOL Low-level output current [^6]|||25|mA
|VOH High-level output voltage [^7]|3.8|||V
|VOL Low-level output voltage [^8]|||0.55|V|
{.dense}

[^6]: This parameter makes the Root CNC controller extremely well suited to drive opto-isolated stepper motor drivers (special sauce)
[^7]: Over full operating specification and at max current draw (-32mA)
[^8]: Over full operating specification and at max current draw (32mA)

### MOSFET Isolation
The Root Controller provides two (Rev 3) or Three (Rev 2.0/2.0) MOSFET controller switches. These switches have their own dedicated input power supply and can be driven from a separate PSU or the same PSU as `V` to allow for greater flexibility. The output are isolated internally to allow switching over noisey equipment, such as solinoides or other inductive switching elements.

| **Parameter** | **Min** | **Typ** | **Max** |**Unit**|
|--|--|--|--|--|
| Vin (`V_F` wrt `0V_F`) | 12|15|36|V|
|Current (Fuse Protected) [^9]|0.001  ||[^10]|A|
{.dense}
[^9]: Current is dependant of the peripherals you connect to the controller
[^10]: Controller has an internal fuse - Rating is 35A

### Relay 
The Root controller has three NO relays (the Normally closed Pole is not accessible). These are design to allow the user to switch large main powered loads, such as Dust extraction, compressors and even lighting.
| **Parameter** | **Min** | **Typ** | **Max** |**Unit**|
|--|--|--|--|--|
| Switch Voltage DC| ||300|V|
| Switch Voltage AC| ||440|V|
|Contact Resistance|||100|mOhm|
|Switch Current (Resistive Load)|||12|A|
|Max Switch Power|||3000|VA|
|Endurance (Switch Cycles)|||1x10^7||
{.dense}

### USB
The USB port on the Root controller is a Type-C 2.0 UFP. 

>This port is also isolated with the `0V`
{.is-info}

| **Parameter** | **Min** | **Typ** | **Max** |**Unit**|
|--|--|--|--|--|
| Voltage (`V_USB` to `0V_USB`) |4.5 |5|5.5|V|
| Current| 5|8|10|mA|
| Data Rate| ||12|Mbps|
|DC Basic Isolation  |||849|V|
|AC Bipolar Basic Isolation  |||849|V|
|AC Unipolar Basic Isolation  |||560|V|
{.dense}

# Software Configurations
For basic configurations for your machine, please see the sub folder names "Configurations"

# Mechanical dimensions

# Tabs {.tabset}
## Rev 3

## Rev 2.1/2.0
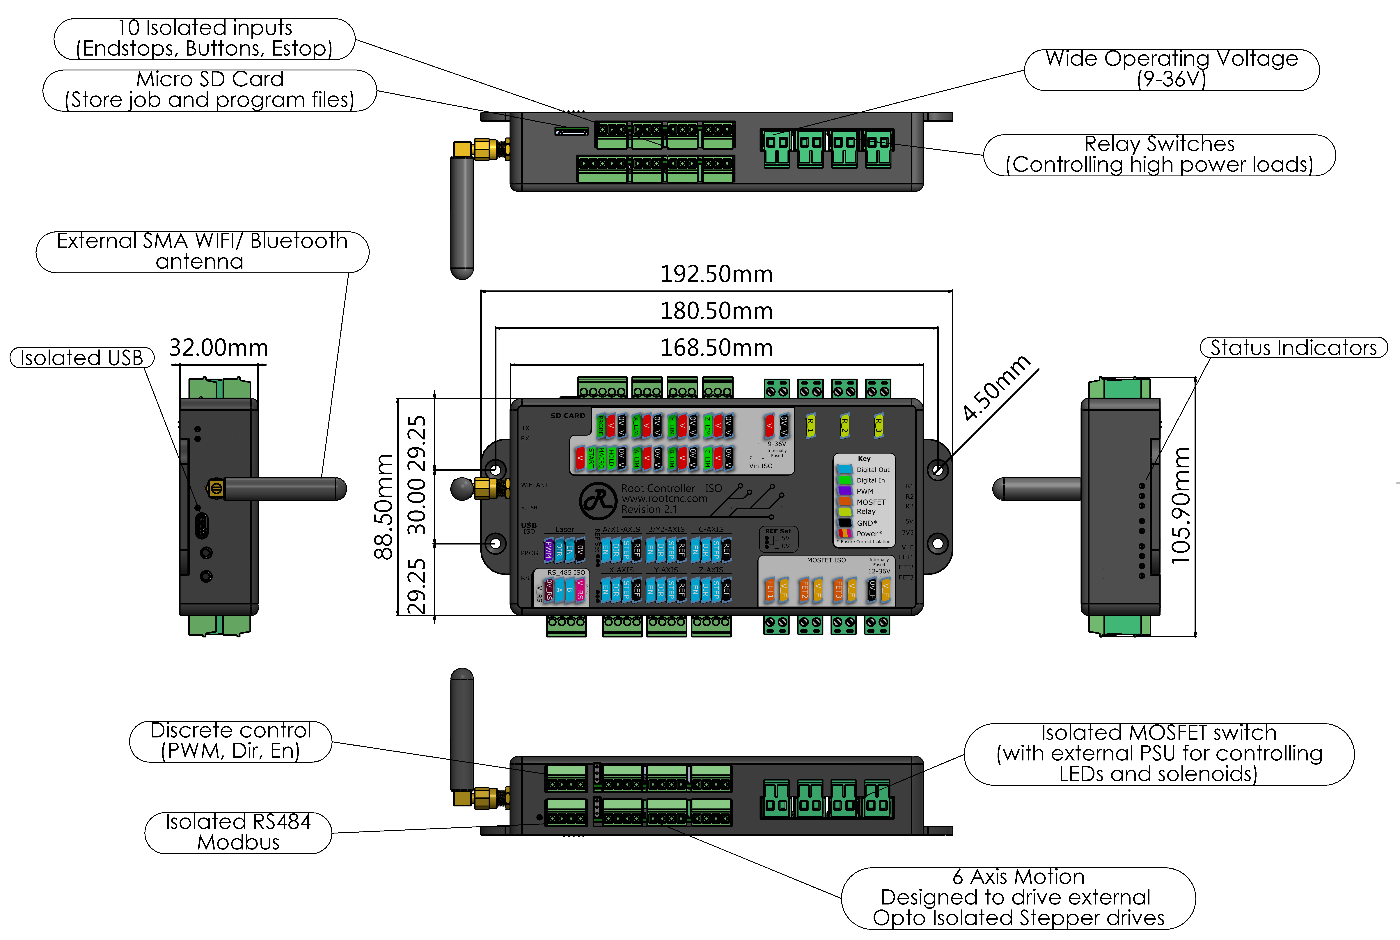
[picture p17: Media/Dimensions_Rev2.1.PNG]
Root Controller Rev 2.0 dimensions

# PCB layout
# Tabs {.tabset}
## Rev 3

## Rev 2.1/2.0
Root Controller Rev 2.0 PCB Layout

# 3D CAD Models

# Tabs {.tabset}
## Rev 3
Comming soon
## Rev 2.1/2.0
Comming soon
# Social links

 1. [Facebook Group](https://www.facebook.com/groups/rootcnc/) 
 2. [Discourse](https://rootcnc.discourse.group/) 
 3. [Discord](https://discord.gg/93Ue5SwthW) Great for quick answer to questions and firmware support
 4. [Thingiverse](https://www.thingiverse.com/sailorpete/designs) 
 5. [Youtube](https://www.youtube.com/c/sailorpete12/)

# License

This project is licensed under the Creative Commons 4.0 license with 
Attribution-NonCommerial-ShareAlike see `LICENSE.txt` for details

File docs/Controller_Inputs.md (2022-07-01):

---
title: Controller Inputs
description: Root Controller Input Section
published: true
date: 2022-05-29T20:56:11.673Z
tags: root controller
editor: markdown
dateCreated: 2022-03-14T22:22:48.038Z
---

# Inputs
The Root controller ISO has isolated inputs which are referenced to the Vin section of the card. Please take note of the isolation boundaries when connecting up the inputs.

The Controller is designed to support normal volt-free switch; such as mechanical switches, either NC (normally closed) or NO (normally open); And/Or NPN inductive sensors. All inputs are electrically the same. For ease of wiring, all axis limit inputs have the same connector and pin out. 

The inputs which are used for “start”, “hold” and “macro” do have a different connector, so please take note of the difference in wiring. Again easy to wiring, Root CNC offer a easy button/ probe point PCB. These can be purchased from the store or downloaded from GitHub.

All inputs are software configured and can be repurposed.

- x6 axis inputs (one per axis, min and max can be combined onto on input. Please see the end stop section for more information)
- x1 probe point
- x3 user configurable inputs (these are typically used for GRBL or fluidnc control signals such as Start, Hold, Reset and Macros.

In total there are *ten* software configurable inputs which can be used for any function.

## Endstops
As mentioned in the pervious section, the Root controller is designed to accommodate voltage free switches, such as mechanical lever switches or NPN inductive switches.

Each input can have two sensors/ switches connected to it, these are typically used on axis with min and max limit switches.

### Inductive Probe Wiring 
> NPN Inductive Switch sensor ONLY {.is-info}



### Inductive Probe Min & Max Wiring 
Image comming soon

### Basic Endstop Wiring
In this basic configuration, either NO (Normally Open) Or NC (Normally Closed) switches can be used


### Endstop wiring Min & Max (NO)


### Endstop wiring Min & Max (NC)

> Please note - NC switches are not recommend on `Y_lim`. IF YOU INTEND TO FLASH THE ROOT CONTROLLER WHILST BEING INSTALLED IN A SYSTEMS. pulling these pins LOW stops the programming routing. If you do use NC switched: then, please ensure these are disconnected piror to programming. 
{.is-warning}

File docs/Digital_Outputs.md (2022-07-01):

---
title: Root Controller Outputs
description: Output options
published: true
date: 2022-03-18T16:33:14.847Z
tags: root controller
editor: markdown
dateCreated: 2022-03-18T16:32:01.131Z
---

# Outputs
Aside from the digital outputs of the stepper driver port (Please see [Controller-Stepper](/Controller-Stepper) for more information). The Root Controller has the additional outputs:

- 3x MOSFET output, great for turning lights or solenoids  on/off
- 3x High power relays output, perfectly suited for turning shop vacs on or dust extractors
- Laser/ spindle port, perfect for controlling a PWM device

## MOSFETS
The Root controller has three high power MOSFETs which can be used to switch the power to a number of device, such as solenoids, lights and DC motors. 

The power supply is fed by its dedicated power connector. The input power is internally fused for added protection. The supply can be separate or tied to other supplies depending on your configuration.

The MOSFET area is perfectly suited for switching inductive loads such a solenoids or relays. 

MOSFET control
- FET_1 - on/off control
- FET_2 - on/off control 
- FET_3 - on/off control


> Please note depending on the software configuration, not all MOSFET or RELAY output can be used at the same time.
{.is-info}

## Relay output 
The Root controller has three relays outputs which can be used to switch high power loads, such as dust extractors, fume extractors and vacum cleaners. 

These relays are capable of switching mains power with a current of mmmm.

Relay control
- R_1 - on/off control
- R_2 - on/off control 
- R_3 - on/off control


> Please note depending on the software configuration, not all MOSFET or RELAY output can be used at the same time.
{.is-info}

## PWM laser/ Spindle output
The Root controller has a discrete output port which can be used to control a number of different devices. For example: lasers, and discrete control spindles.

Laser/ Spindle control
- EN - on/off control
- DIR - on/off control 
- PWM - on/off control & PWM Control


> For spindle control, it is advised you use a MODBUS/ RS485 VFD and communicated through the isolated spindle interface.
{.is-info}

> This port is NOT isolated so careful consideration is needed when connecting external devices to ensure the isolation zones are not violated
{.is-warning}

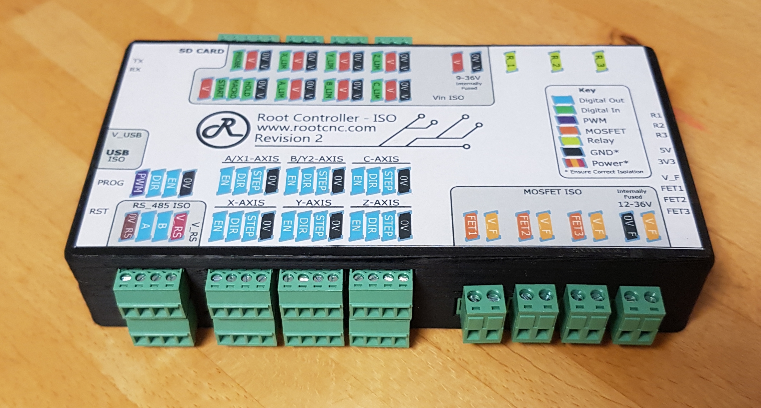
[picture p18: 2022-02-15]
Media/RootControllerISO-R2.0.jpg

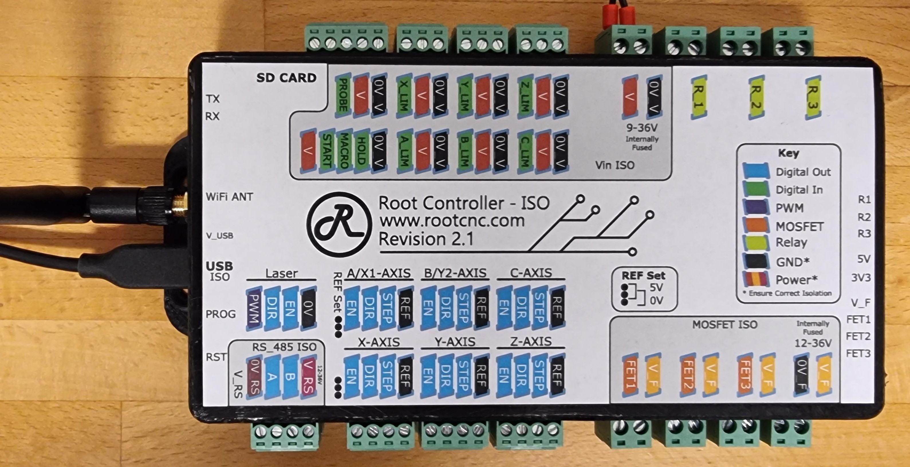
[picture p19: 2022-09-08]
Media/ex_20220321_224951.jpg

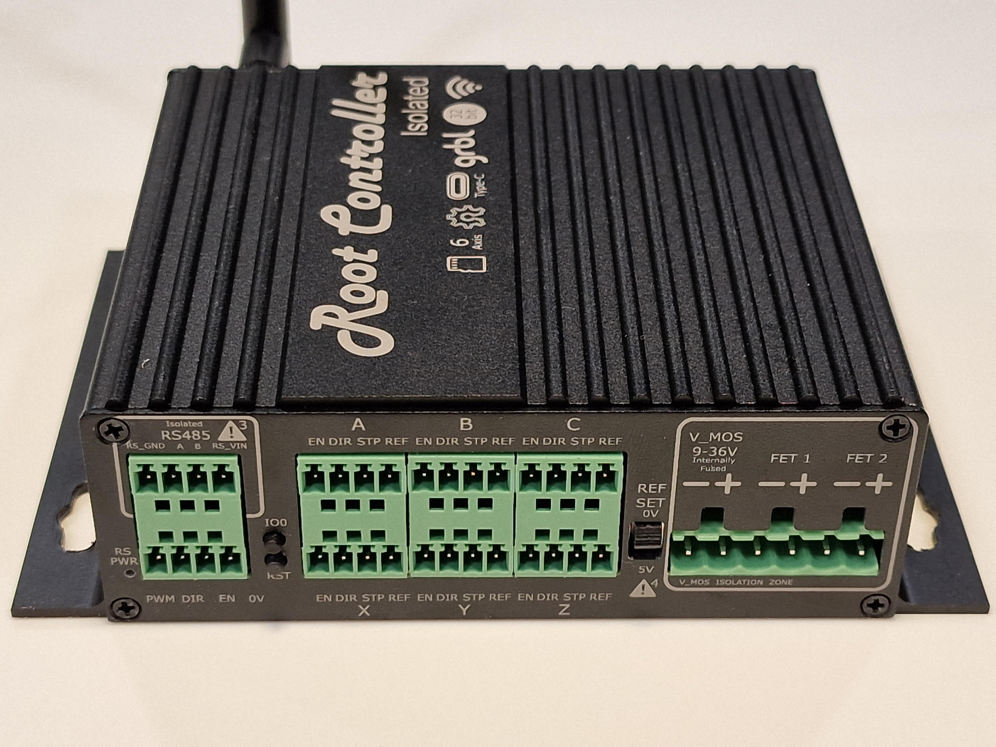
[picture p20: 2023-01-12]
Media/ControllerR3_2.jpg

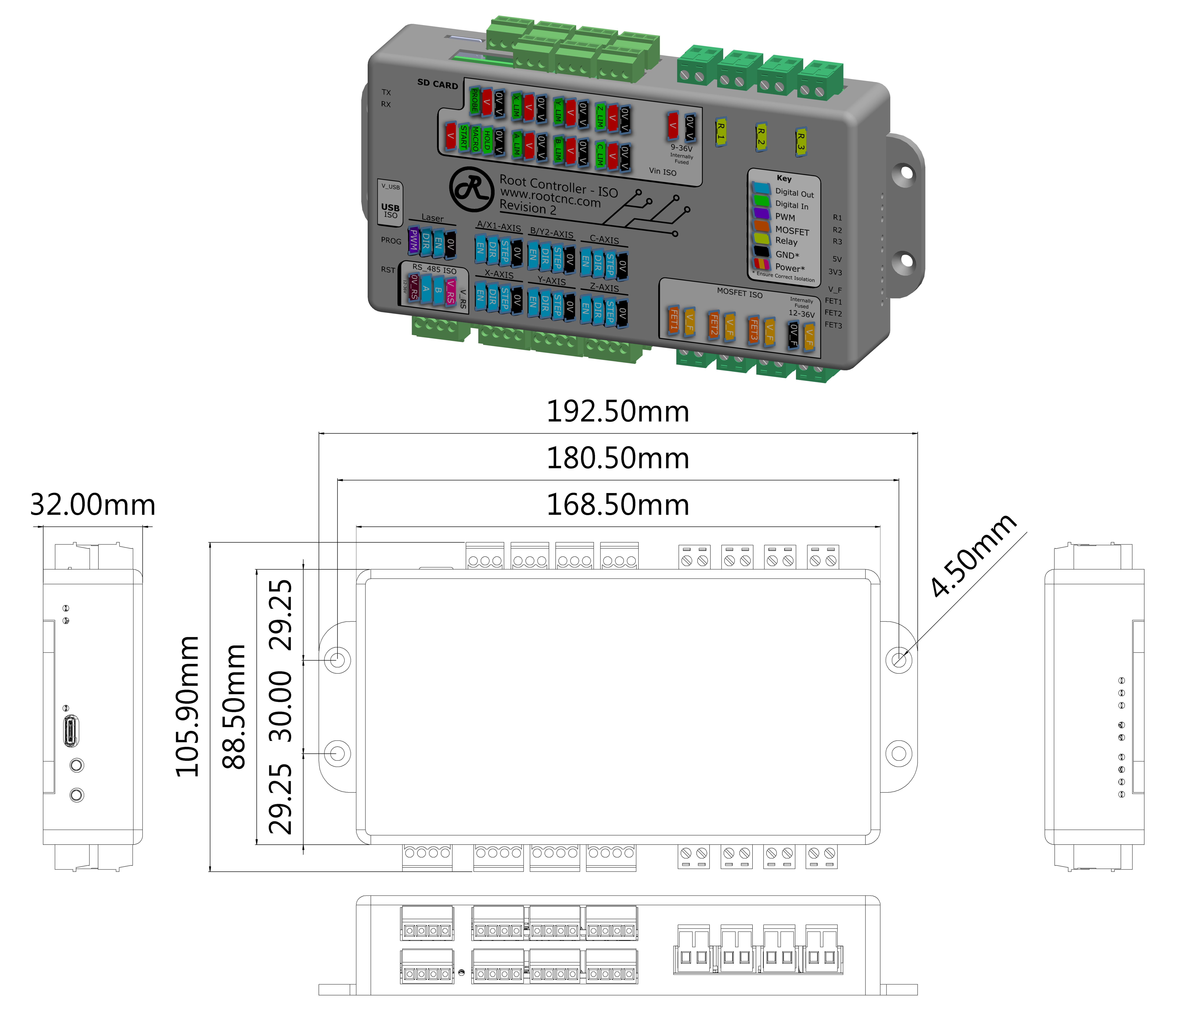
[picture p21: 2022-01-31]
Media/Dimensions_Rev2.0.PNG

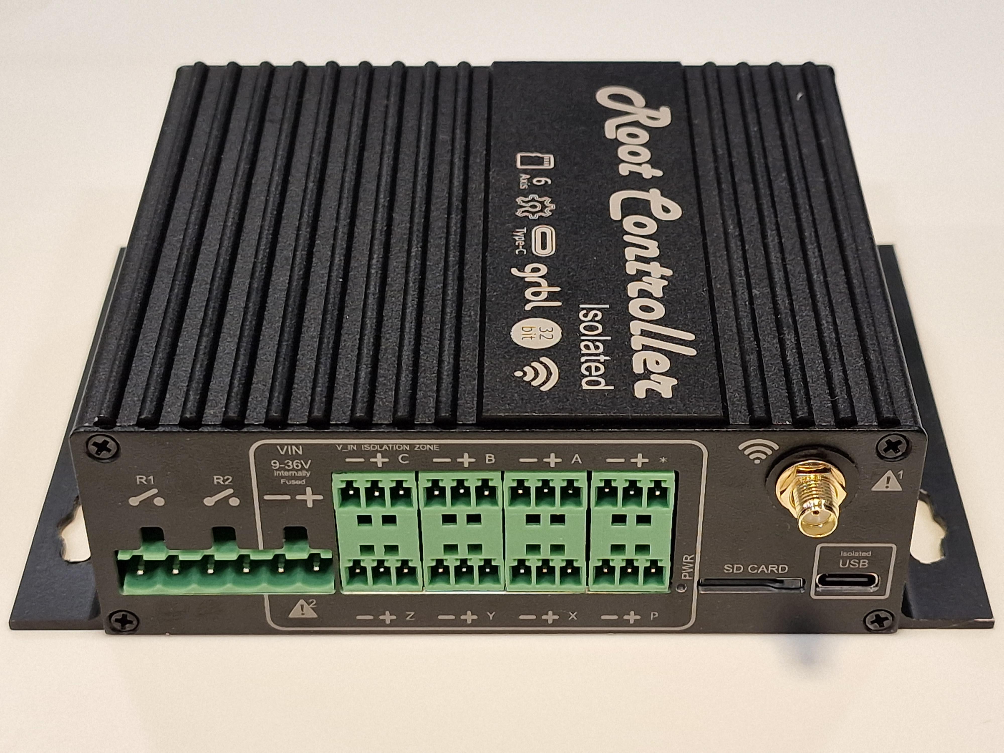
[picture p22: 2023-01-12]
Media/ControllerR3_3.jpg

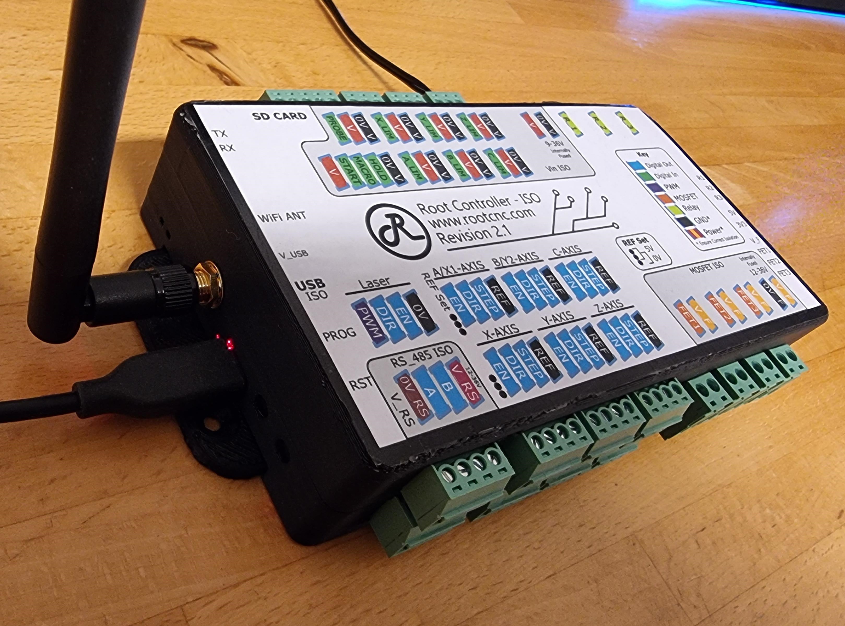
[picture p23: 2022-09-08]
Media/ex_20220321_224927.jpg

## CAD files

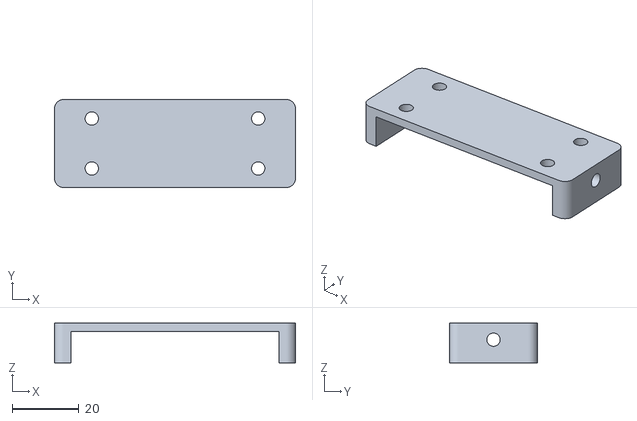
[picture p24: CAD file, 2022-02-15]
Button_Probe/ButtonMount-Base.STL
72.4 x 26.4 x 12.0

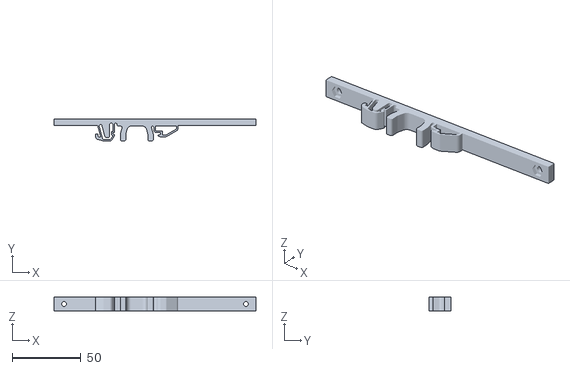
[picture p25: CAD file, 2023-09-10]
STL/PlasticCase_DIN_Mount_Rev3.stl
147.1 x 16.0 x 10.0

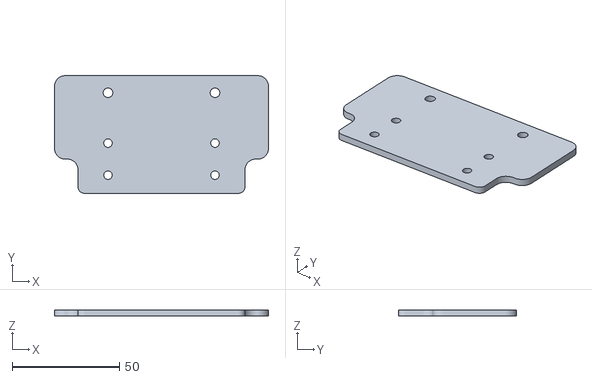
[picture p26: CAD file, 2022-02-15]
Button_Probe/ButtonMount-R4Extender.STL
100.0 x 55.0 x 3.00

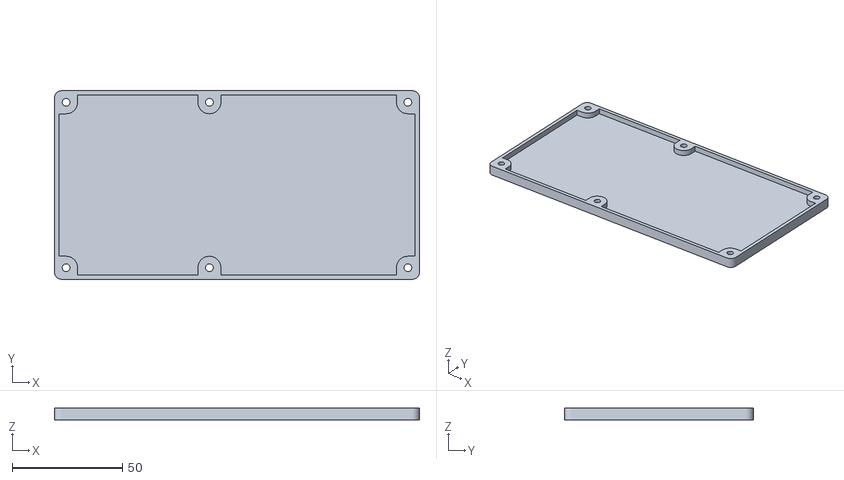
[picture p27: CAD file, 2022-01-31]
STL/PlasticCase_Base_Rev2-0.STL
165.5 x 85.5 x 5.45

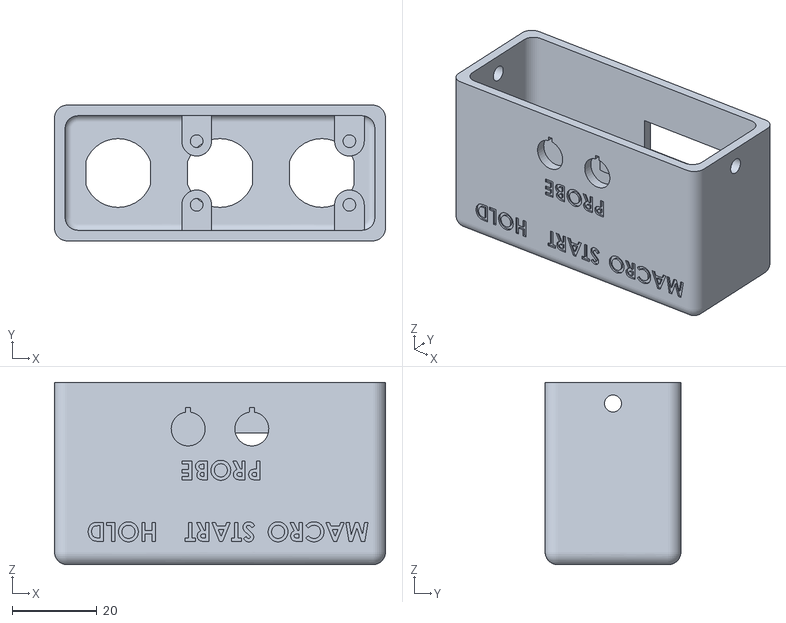
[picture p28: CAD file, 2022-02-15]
Button_Probe/ButtonMount-Top-Macro-Start-Hold.STL
78.0 x 32.0 x 43.0

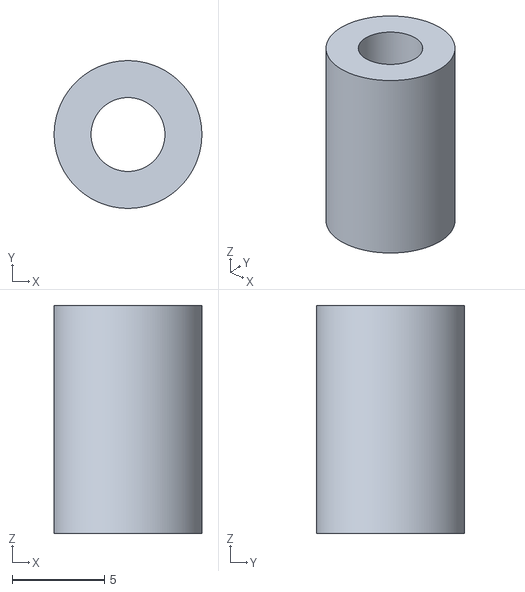
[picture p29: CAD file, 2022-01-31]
STL/PlasticCase_Spacer_Rev2-0.STL
8.00 x 8.00 x 12.4

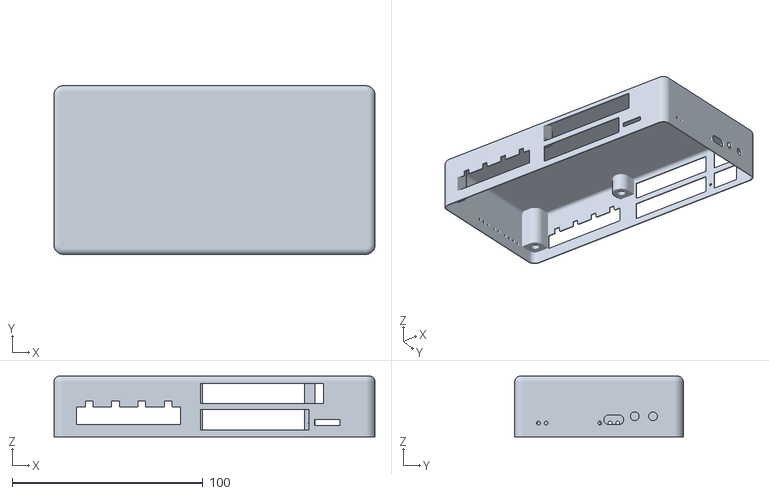
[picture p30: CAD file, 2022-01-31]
STL/PlasticCase_Lid_Rev2-0.STL
168.5 x 88.5 x 32.0

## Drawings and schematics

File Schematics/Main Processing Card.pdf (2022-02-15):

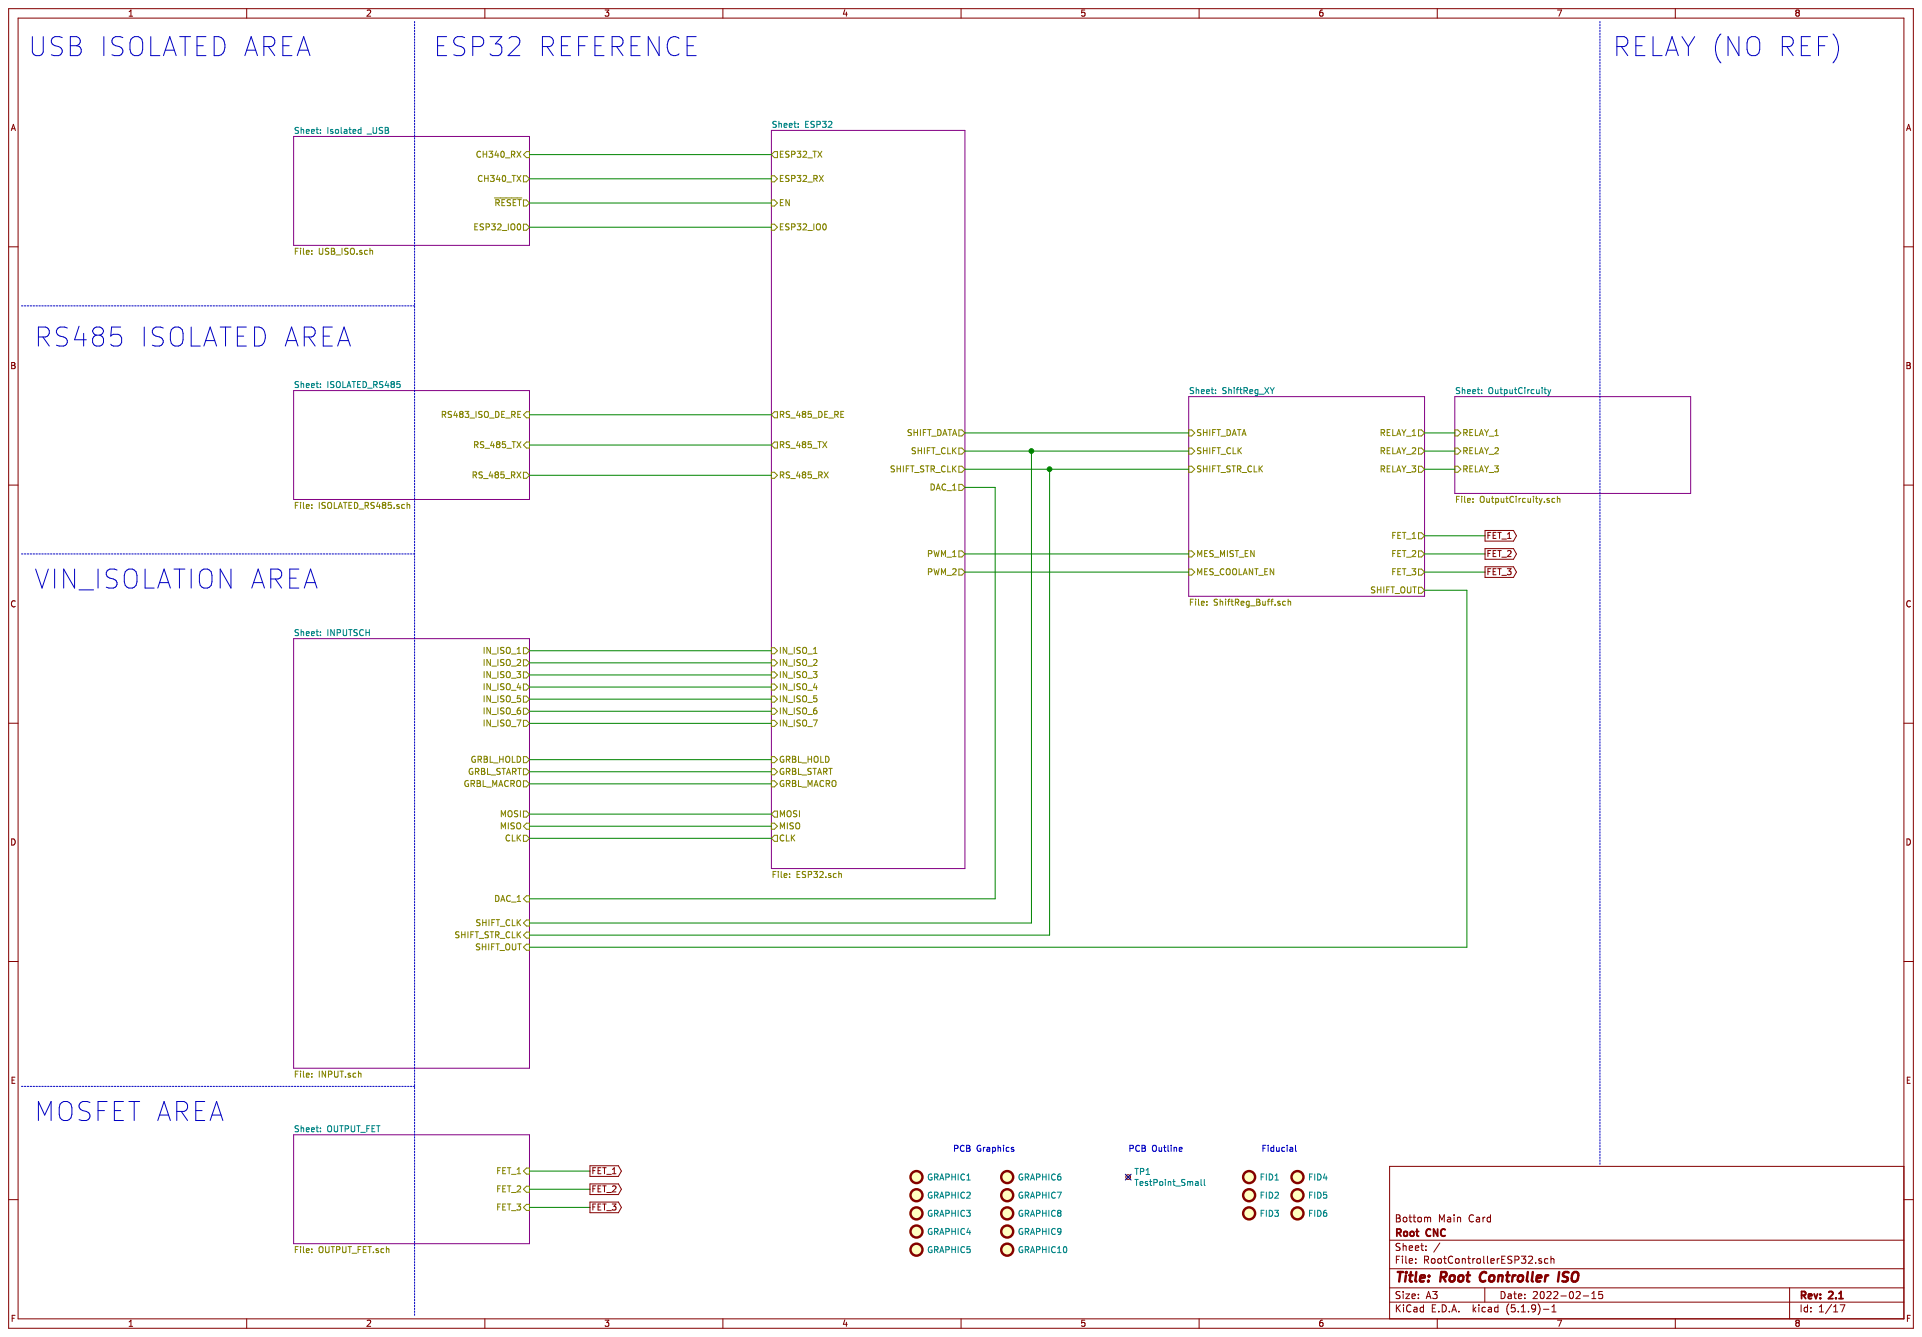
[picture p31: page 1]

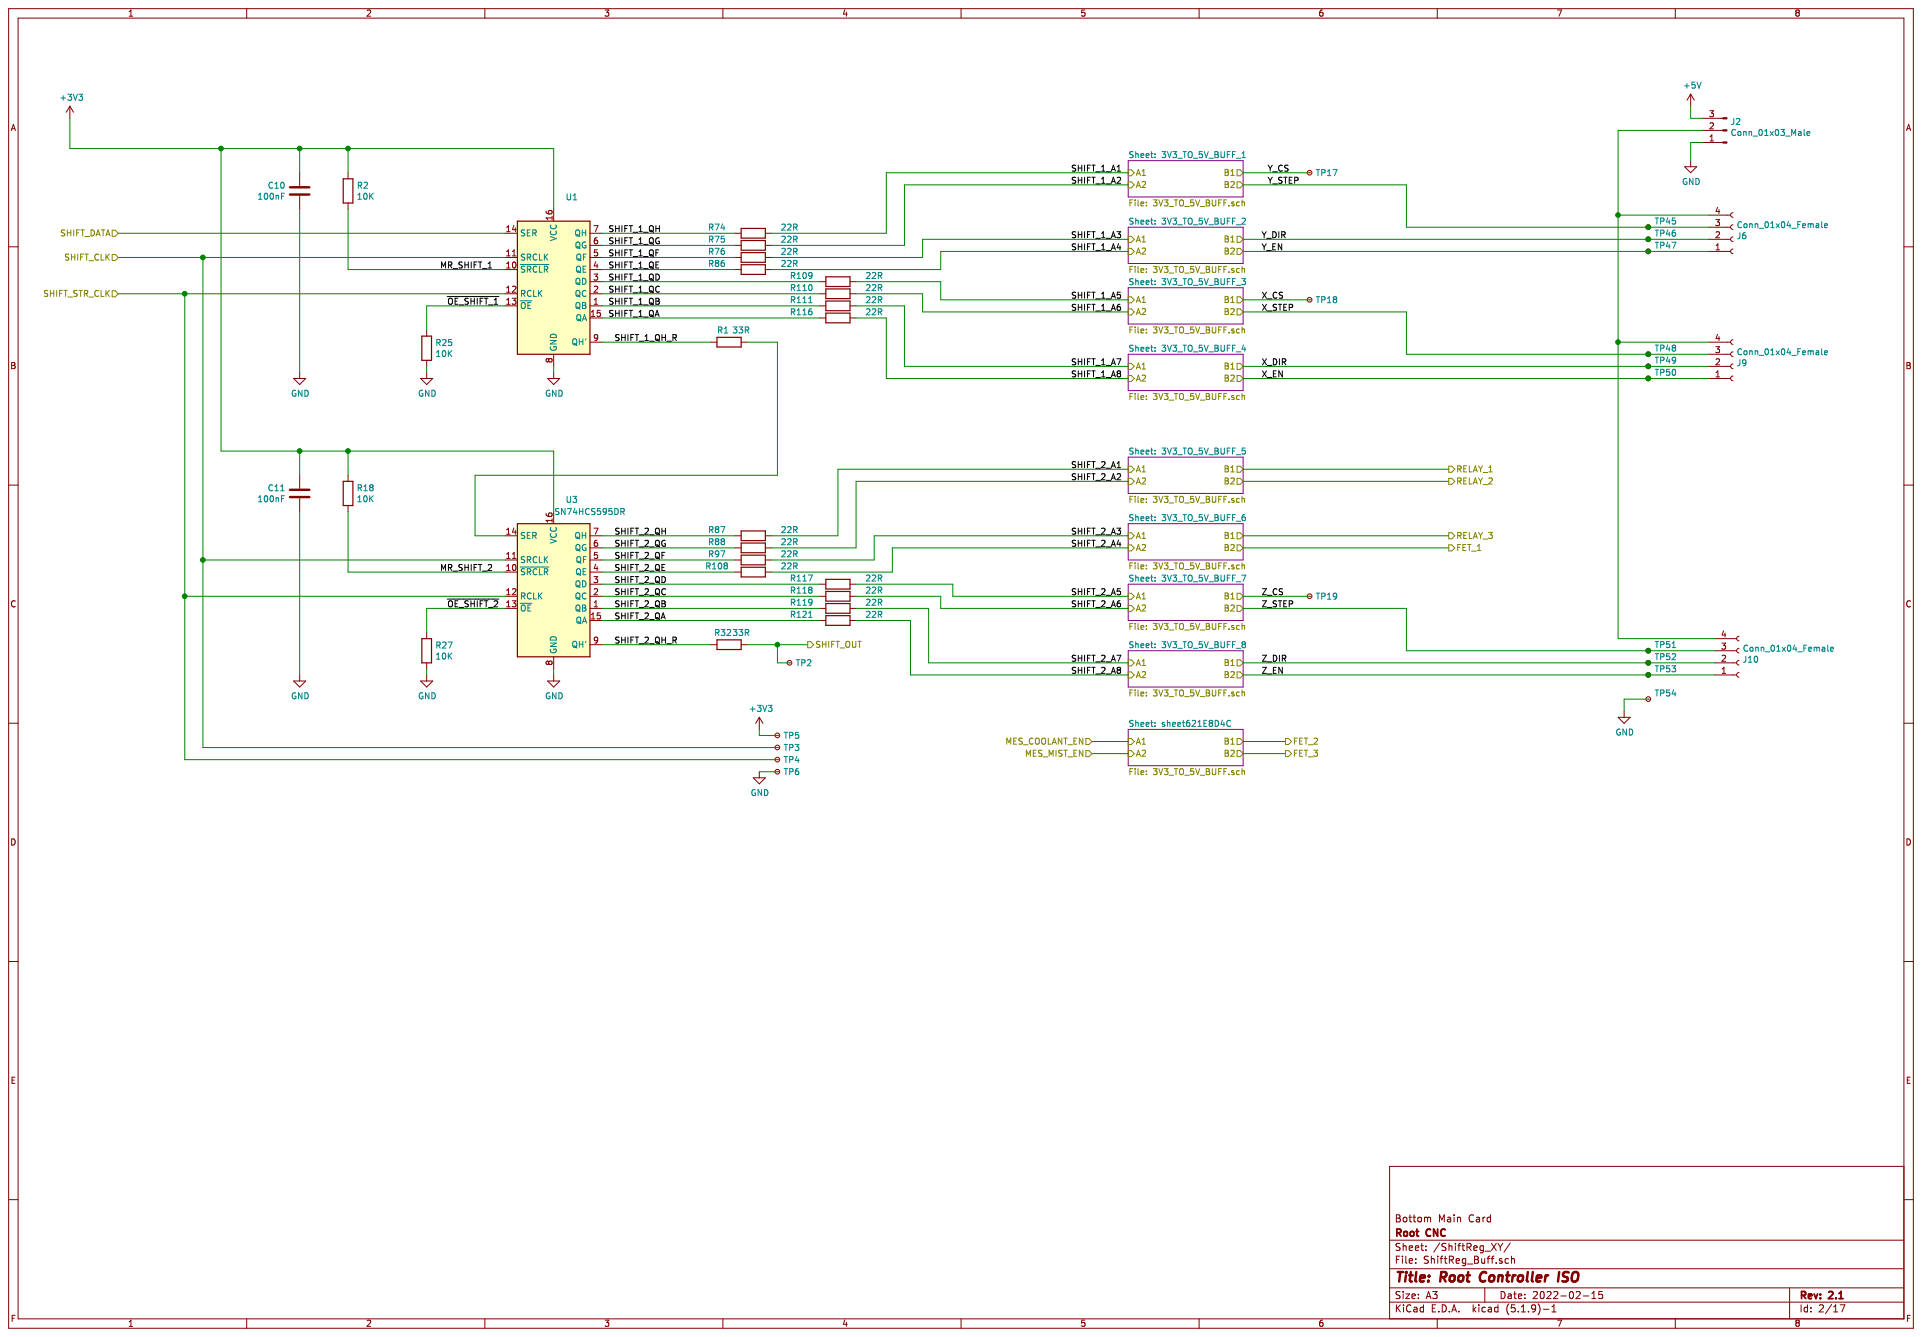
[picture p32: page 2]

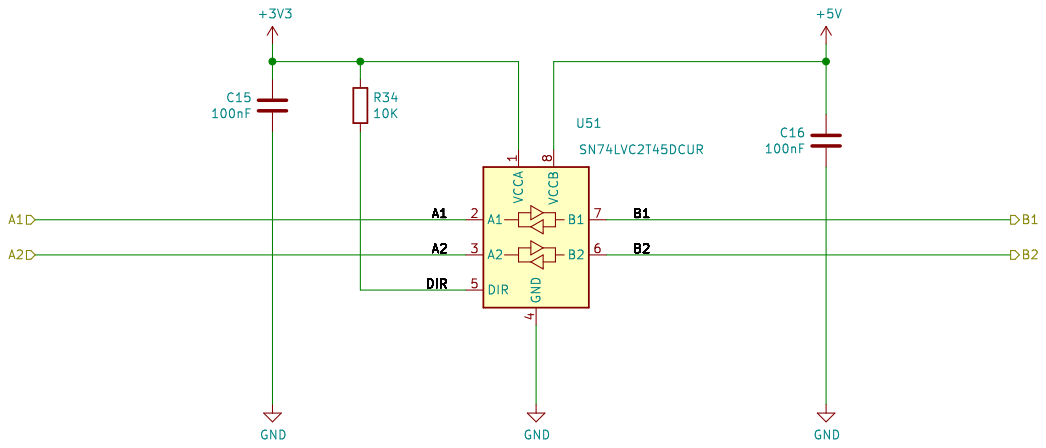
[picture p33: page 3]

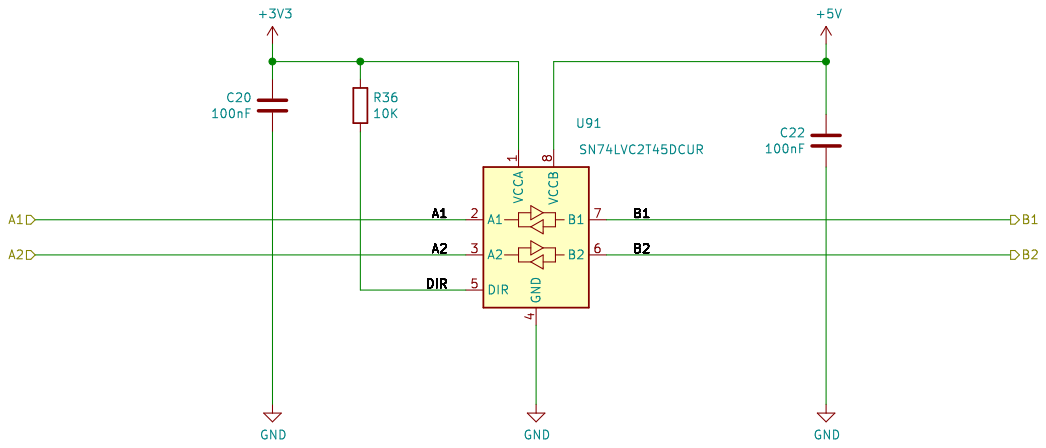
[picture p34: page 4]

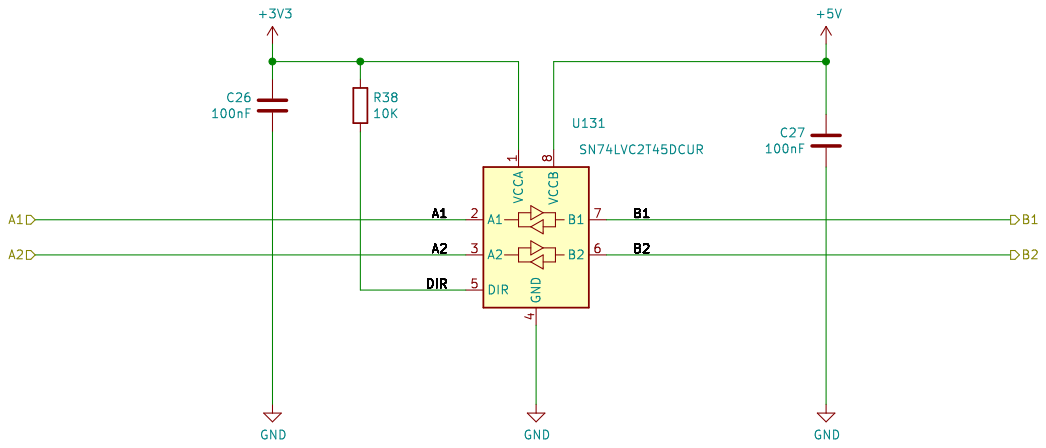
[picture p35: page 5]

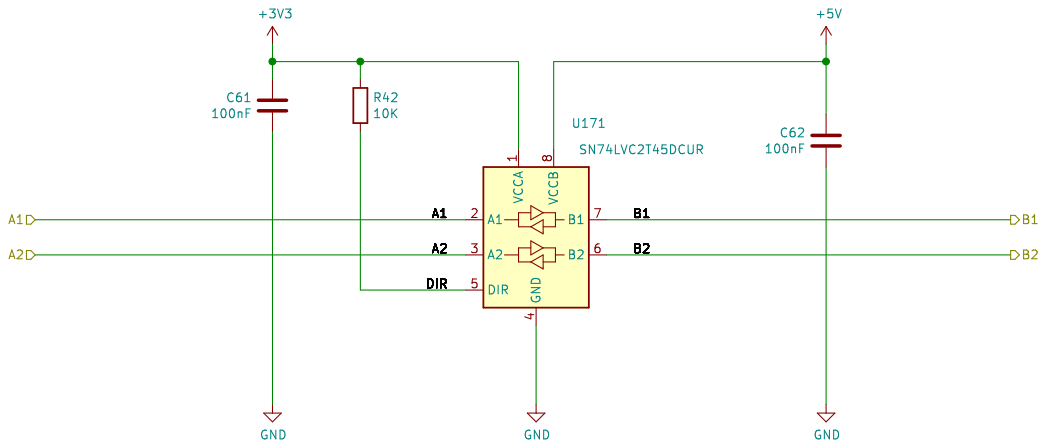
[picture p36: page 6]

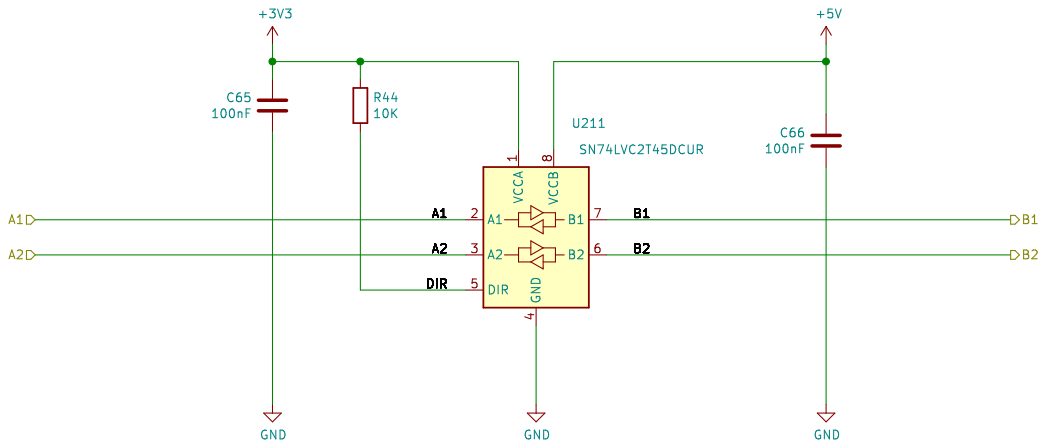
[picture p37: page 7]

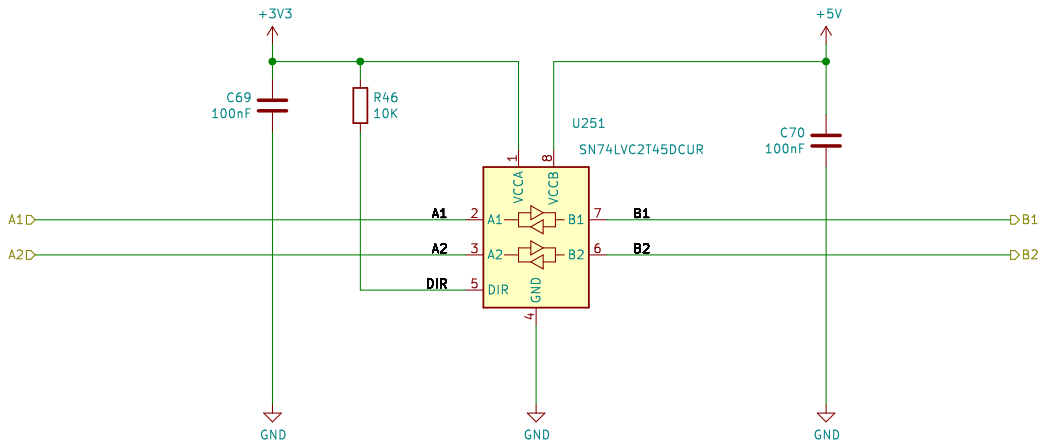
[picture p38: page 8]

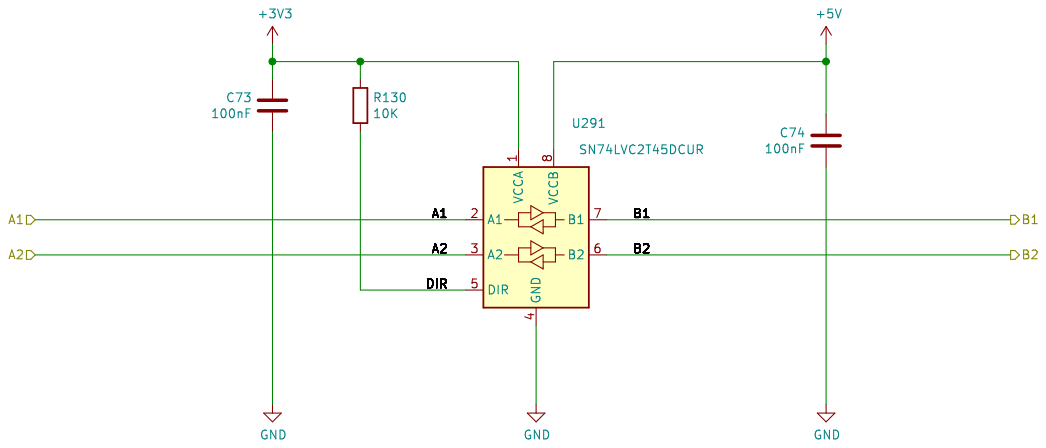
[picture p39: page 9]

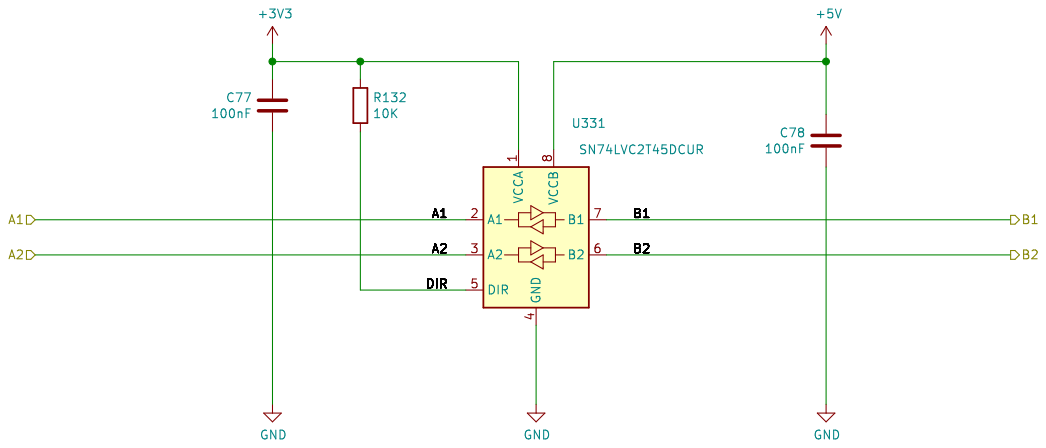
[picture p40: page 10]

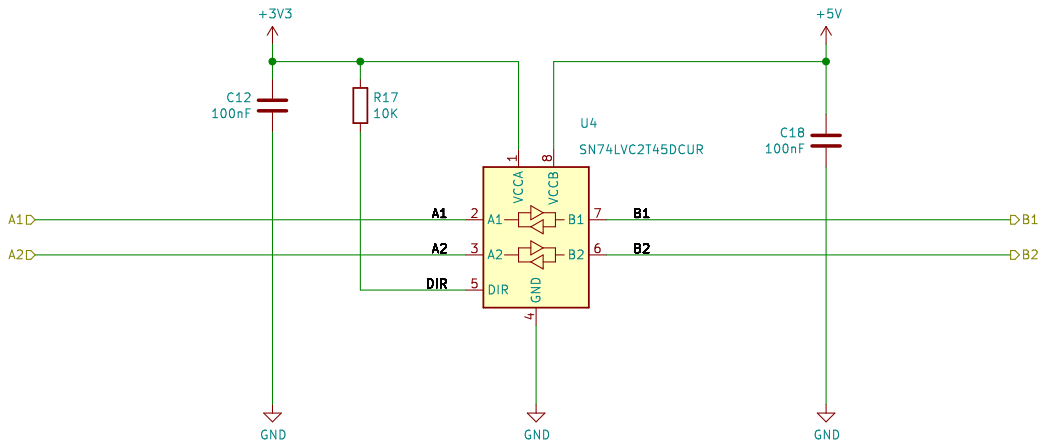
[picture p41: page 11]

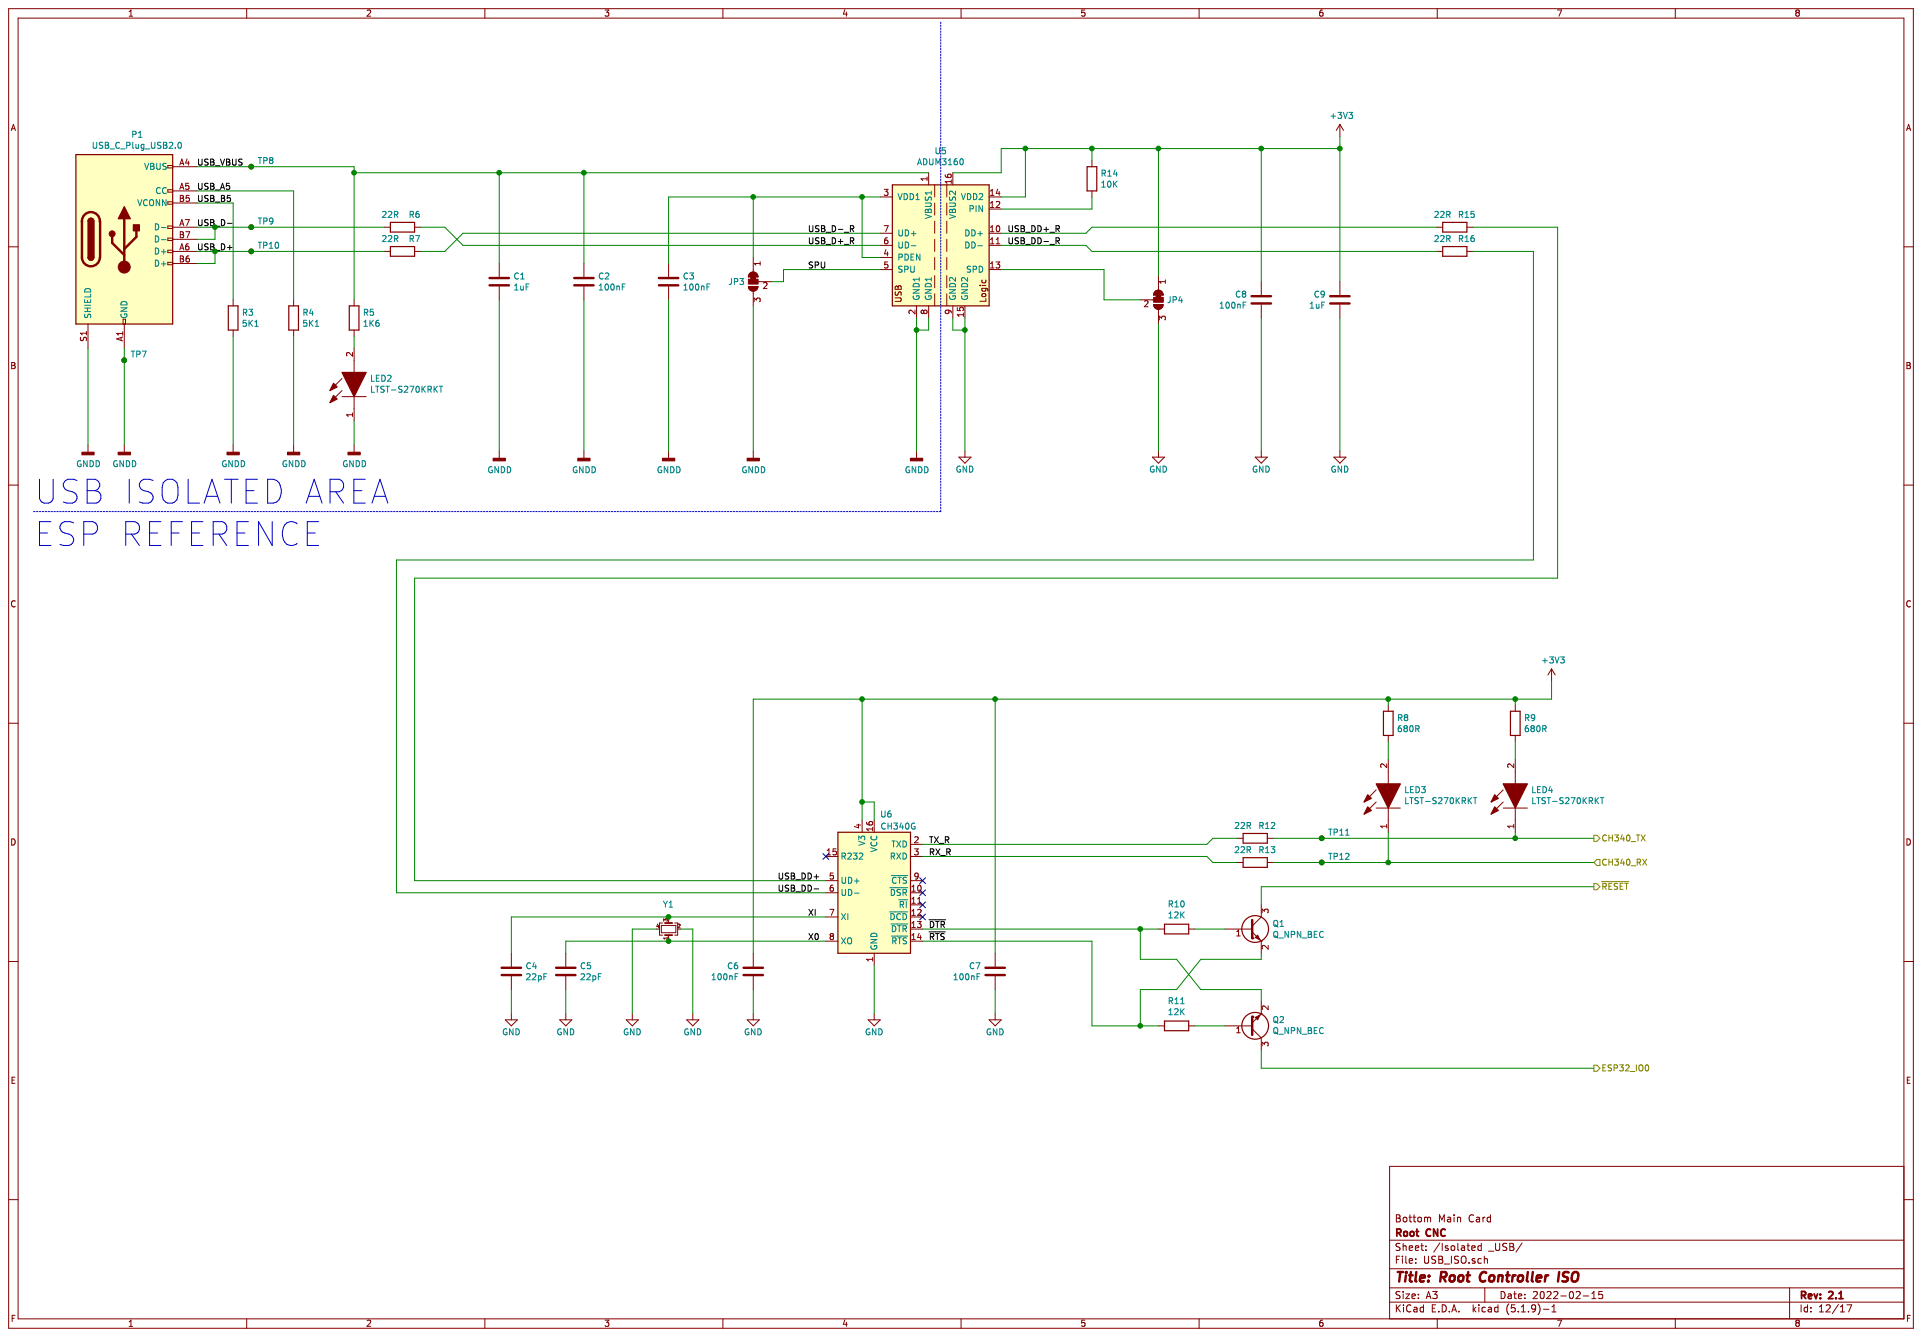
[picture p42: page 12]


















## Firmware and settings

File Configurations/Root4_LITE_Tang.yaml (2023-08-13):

board: Root Controller ISO
name: Root 4 Lite
stepping:
  engine: I2S_STATIC
  idle_ms: 255
  pulse_us: 4
  dir_delay_us: 1
  disable_delay_us: 3

axes:
  shared_stepper_disable_pin: NO_PIN
  x:
    steps_per_mm: 400.000
    max_rate_mm_per_min: 3000.000
    acceleration_mm_per_sec2: 100.000
    max_travel_mm: 218.000
    soft_limits: true
    homing:
      cycle: 2
      positive_direction: true
      mpos_mm: 218.000
      feed_mm_per_min: 100.000
      seek_mm_per_min: 800.000
      settle_ms: 500
      seek_scaler: 1.100
      feed_scaler: 1.100

    motor0:
      limit_neg_pin: NO_PIN
      limit_pos_pin: NO_PIN
      limit_all_pin: gpio.26
      hard_limits: true
      pulloff_mm:1.000
      standard_stepper:
        step_pin: I2SO.2
        direction_pin: I2SO.1:low 
        disable_pin: I2SO.0:high

  y:
    steps_per_mm: 400.000
    max_rate_mm_per_min: 3000.000
    acceleration_mm_per_sec2: 100.000
    max_travel_mm: 278.000
    soft_limits: true
    homing:
      cycle: 2
      positive_direction: true
      mpos_mm: 278.000
      feed_mm_per_min: 100.000
      seek_mm_per_min: 800.000
      settle_ms: 500
      seek_scaler: 1.100
      feed_scaler: 1.100

    motor0:
      limit_neg_pin: NO_PIN
      limit_pos_pin: gpio.02
      limit_all_pin: NO_PIN
      hard_limits: true
      pulloff_mm:1.000
      standard_stepper:
        step_pin: I2SO.6
        direction_pin: I2SO.5
        disable_pin: I2SO.4:high
        
    motor1:
      limit_neg_pin: NO_PIN
      limit_pos_pin: gpio.32
      limit_all_pin: NO_PIN
      hard_limits: true
      pulloff_mm: 1.000
      standard_stepper:
        step_pin: I2SO.26
        direction_pin: I2SO.25
        disable_pin: I2SO.24:high
  z:
    steps_per_mm: 500.000
    max_rate_mm_per_min: 3000.000
    acceleration_mm_per_sec2: 100.000
    max_travel_mm: 59.000
    soft_limits: true
    homing:
      cycle: 1
      positive_direction: true
      mpos_mm: 0.500
      feed_mm_per_min: 100.000
      seek_mm_per_min: 800.000
      settle_ms: 500
      seek_scaler: 1.100
      feed_scaler: 1.100

    motor0:
      limit_neg_pin: NO_PIN
      limit_pos_pin: gpio.15
      limit_all_pin: NO_PIN
      hard_limits: true
      pulloff_mm:1.000
      standard_stepper:
        step_pin: I2SO.10
        direction_pin: I2SO.9:low 
        disable_pin: I2SO.8:high
        
  a:
    steps_per_mm: 444.444
    max_rate_mm_per_min: 3000.000
    acceleration_mm_per_sec2: 250.000
    max_travel_mm: 99999.99
    soft_limits: false
    homing:
      cycle: 2
      positive_direction: true
      mpos_mm: 0.0
      feed_mm_per_min: 3000.000
      seek_mm_per_min: 3000.000
      settle_ms: 500
      seek_scaler: 3.500
      feed_scaler: 1.500

    motor0:
      limit_neg_pin: NO_PIN
      limit_pos_pin: gpio.35:low
      limit_all_pin: NO_PIN
      hard_limits: false
      pulloff_mm:0.1
      standard_stepper:
        step_pin: I2SO.22:low 
        direction_pin: I2SO.21:low 
        disable_pin: I2SO.20:high
i2so:
  bck_pin: gpio.22
  data_pin: gpio.12
  ws_pin: gpio.21

spi:
  miso_pin: gpio.19
  mosi_pin: gpio.23
  sck_pin: gpio.18

sdcard:
  card_detect_pin: NO_PIN
  cs_pin: gpio.5

control:
  safety_door_pin: NO_PIN
  reset_pin: NO_PIN
  feed_hold_pin: gpio.34
  cycle_start_pin: gpio.36
  macro0_pin: gpio.39
  macro1_pin: NO_PIN
  macro2_pin: NO_PIN
  macro3_pin: NO_PIN

coolant:
  flood_pin: gpio.33
  mist_pin: gpio.13
  delay_ms: 0

probe:
  pin: gpio.27
  check_mode_start: true

macros:
  startup_line0:
  startup_line1:
  macro0: 
  macro1: 
  macro2: 
  macro3:
  
user_outputs:
  analog0_pin: NO_PIN
  analog1_pin: NO_PIN
  analog2_pin: NO_PIN
  analog3_pin: NO_PIN
  analog0_hz: 5000
  analog1_hz: 5000
  analog2_hz: 5000
  analog3_hz: 5000
  digital0_pin: i2so.12
  digital1_pin: i2so.13
  digital2_pin: i2so.14
  digital3_pin: i2so.15


start:
  must_home: true

pwm:
  pwm_hz: 2000
  direction_pin: I2SO.16
  output_pin: gpio.25
  enable_pin: I2SO.17
  disable_with_s0: false
  s0_with_disable: true
  spinup_ms: 0
  spindown_ms: 0
  tool_num: 0
  speed_map: 0=0.000% 3500=100.000%

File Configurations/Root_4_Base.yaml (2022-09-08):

board: Root Controller ISO
name: Root 4 V20
stepping:
  engine: I2S_STREAM
  idle_ms: 255
  pulse_us: 4
  dir_delay_us: 1
  disable_delay_us: 3

axes:
  shared_stepper_disable_pin: NO_PIN
  x:
    steps_per_mm: 160.000
    max_rate_mm_per_min: 3700.000
    acceleration_mm_per_sec2: 250.000
    max_travel_mm: 1198.000
    soft_limits: true
    homing:
      cycle: 2
      positive_direction: true
      mpos_mm: 1197.000
      feed_mm_per_min: 100.000
      seek_mm_per_min: 2000.000
      settle_ms: 1000
      seek_scaler: 10.00
      feed_scaler: 10.00

    motor0:
      limit_neg_pin: NO_PIN
      limit_pos_pin: NO_PIN
      limit_all_pin: gpio.26:low
      hard_limits: true
      pulloff_mm:2.000
      standard_stepper:
        step_pin: I2SO.2
        direction_pin: I2SO.1:high 
        disable_pin: I2SO.0:low

  y:
    steps_per_mm: 160.000
    max_rate_mm_per_min: 3700.000
    acceleration_mm_per_sec2: 250.000
    max_travel_mm: 1185.000
    soft_limits: true
    homing:
      cycle: 3
      positive_direction: true
      mpos_mm: 1185.000
      feed_mm_per_min: 100.000
      seek_mm_per_min: 2000.000
      settle_ms: 1000
      seek_scaler: 1.100
      feed_scaler: 5.500

    motor0:
      limit_neg_pin: NO_PIN
      limit_pos_pin: gpio.32:low
      limit_all_pin: NO_PIN
      hard_limits: true
      pulloff_mm:1.000
      standard_stepper:
        step_pin: I2SO.6
        direction_pin: I2SO.5:low
        disable_pin: I2SO.4:low
        
    motor1:
      limit_neg_pin: NO_PIN
      limit_pos_pin: gpio.35:low
      limit_all_pin: NO_PIN
      hard_limits: true
      pulloff_mm: 3.120
      standard_stepper:
        step_pin: I2SO.22
        direction_pin: I2SO.21:low
        disable_pin: I2SO.20:low
  z:
    steps_per_mm: 160.000
    max_rate_mm_per_min: 4500.000
    acceleration_mm_per_sec2: 500.000
    max_travel_mm: 159.000
    soft_limits: true
    homing:
      cycle: 1
      positive_direction: true
      mpos_mm: 0.500
      feed_mm_per_min: 100.000
      seek_mm_per_min: 1000.000
      settle_ms: 500
      seek_scaler: 1.100
      feed_scaler: 1.500

    motor0:
      limit_neg_pin: NO_PIN
      limit_pos_pin: gpio.15:low
      limit_all_pin: NO_PIN
      hard_limits: true
      pulloff_mm:1.000
      standard_stepper:
        step_pin: I2SO.10
        direction_pin: I2SO.9:high 
        disable_pin: I2SO.8:low
        

i2so:
  bck_pin: gpio.22
  data_pin: gpio.12
  ws_pin: gpio.21

spi:
  miso_pin: gpio.19
  mosi_pin: gpio.23
  sck_pin: gpio.18

sdcard:
  card_detect_pin: NO_PIN
  cs_pin: gpio.5

control:
  safety_door_pin: NO_PIN
  reset_pin: NO_PIN
  feed_hold_pin: gpio.34
  cycle_start_pin: gpio.36
  macro0_pin: gpio.39
  macro1_pin: NO_PIN
  macro2_pin: NO_PIN
  macro3_pin: NO_PIN

coolant:
  flood_pin: gpio.33
  mist_pin: gpio.13
  delay_ms: 0

probe:
  pin: gpio.27
  check_mode_start: true

macros:
  startup_line0:
  startup_line1:
  macro0: 
  macro1: 
  macro2: 
  macro3:
  
user_outputs:
  analog0_pin: NO_PIN
  analog1_pin: NO_PIN
  analog2_pin: NO_PIN
  analog3_pin: NO_PIN
  analog0_hz: 5000
  analog1_hz: 5000
  analog2_hz: 5000
  analog3_hz: 5000
  digital0_pin: i2so.12
  digital1_pin: i2so.13
  digital2_pin: i2so.14
  digital3_pin: i2so.15


start:
  must_home: true
  
SiemensV20:
  uart:
    txd_pin: gpio.17
    rxd_pin: gpio.16
    rts_pin: gpio.4
    baud: 9600
    mode: 8E1
  modbus_id: 1
  tool_num: 0
  speed_map: 0=0% 24000=100%

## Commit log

2020-06-24 First Upload
    [ESP32_ROOT_4_PINOUT.xlsx]
2021-07-28 Added Case files for Beta Cards
    [CaseLid_Bottom.STL, CaseLid_Top.STL, DIN_Rail_Clip.STL]
2022-01-31 Added Rev 2 Case
    [PlasticCase_Base_Rev2-0.STL, PlasticCase_Lid_Rev2-0.STL, PlasticCase_Spacer_Rev2-0.STL]
2022-01-31 removed Beta
    [CaseLid_Bottom.STL, CaseLid_Top.STL, DIN_Rail_Clip.STL]
2022-02-02 Update to probe
2022-02-15 Added Button case and schematics
    [ButtonMount-Base.STL, ButtonMount-R4Extender.STL, ButtonMount-Top-Macro-Start-Hold.STL]
2022-06-28 Updated Pin information
    [ESP32_ROOT_4_PINOUT.xlsx]
2023-01-05 Update Pinout.md
    Updated Pin out to include the new Rev 3 version
2023-01-11 Added images to the stepper wiring
2023-01-12 Updated Wiki and added PCB photo
2023-12-05 Add example wiring of RS485 on a Huanyang VFD
